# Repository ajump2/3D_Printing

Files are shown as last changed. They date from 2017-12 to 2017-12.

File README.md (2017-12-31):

# Introduction
I'm running a modified Prusa i3 using two e3D v6s on a Bowden setup, originally this printer was built from a reprapguru kit found [here](https://reprapguru.com/). Any and all gcode is made using Slicer or Cura, and modified using a text editor so the fan runs constantly.

# Bowden Dual Extruder Installation
## 3D-Printed Parts
* 2 x [extruder mounts](https://www.thingiverse.com/thing:2078038)
* 2 x [x-carriage mount](https://www.thingiverse.com/thing:1065471)

The x-carriage mount fits the standard Prusa i3 x-carriage, like the one modeled [here](https://www.thingiverse.com/thing:399130) (So no need to install a new x-carriage). I'm also gonna suggest that you print two of the x-carriage mounts, in case one breaks.

## Materials
* Additional Extruder motor (I repurposed the ones from [here](https://www.amazon.com/Geeetech-Dual-Extruder-hotend-nozzle/dp/B075TGY28F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), and you can use the direct drive system if you'd like, although I had a number of issues with it)
* 1 x [RRD fan extender](https://www.amazon.com/AuBreey-Extender-DUAL-EXTRUSION-Printer-Reprap/dp/B07115SX39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)
* 2 x [PTFE fittings](https://www.amazon.com/dp/B01F1XTRGI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)
* 2 x [e3d v6s](https://www.amazon.com/E3D-All-metal-HotEnd-Full-Approximately/dp/B00NAK9JFO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)

Please note that while these parts satisfy the minimum requirement, redundancies are recommended. The e3D thermistors are sensitive, and can crack very easily. Also note that you'll want to heat the hot ends up before removing the heat breaks (which you'll have to do as you're troubleshooting).

## Electronic/Mechanical Configuration
In-Progress

### Wiring
The RRD extender fits on the Aux 1 pins, where you can follow the below diagram for wiring.

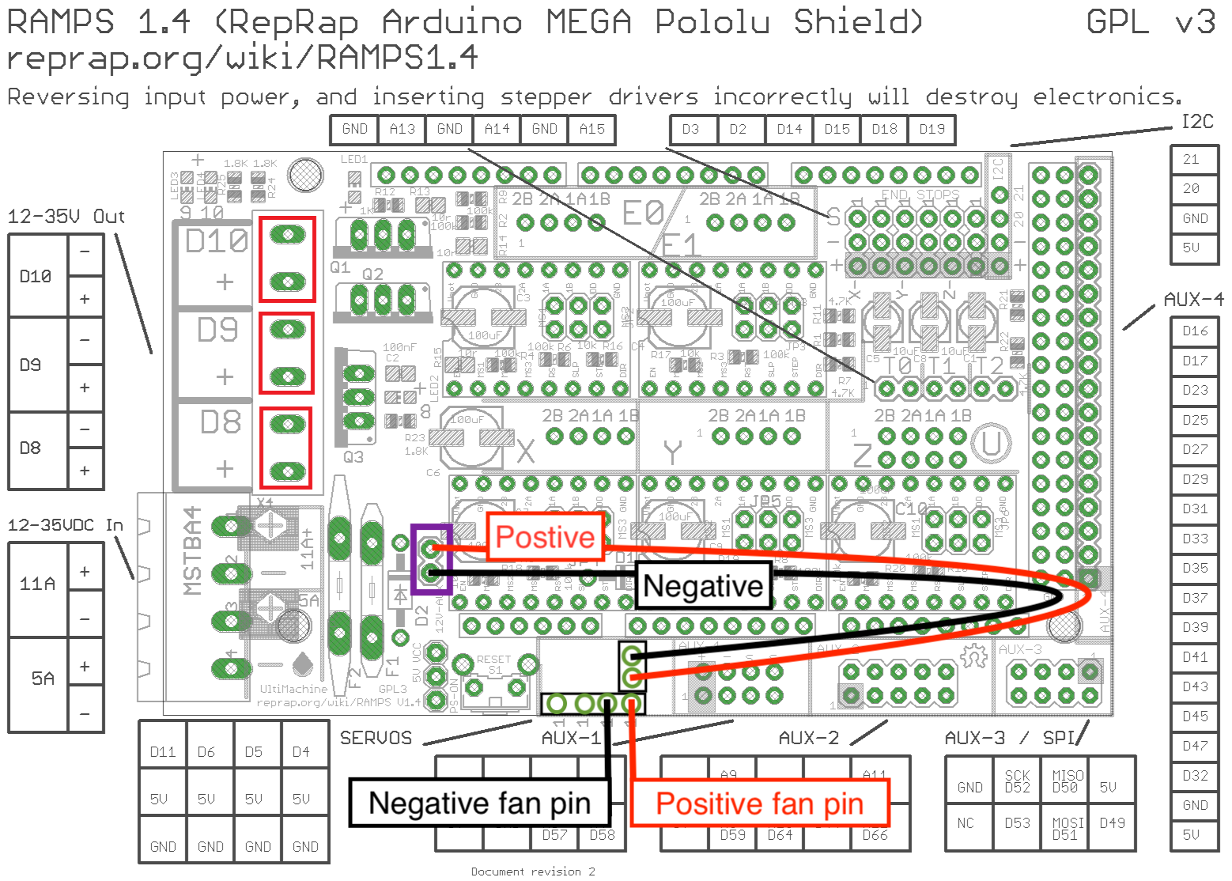
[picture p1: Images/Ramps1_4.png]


This frees the D9 pin (where the fan was connected) for use by the second extruder heater cartridge. As with the first extruder, polarity is not important. The extruder motor connects to the E1 pins (above where the first extruder is connected). Then you'll want to connect the second extruders thermistor to space T2. This can all be seen in the below diagram.

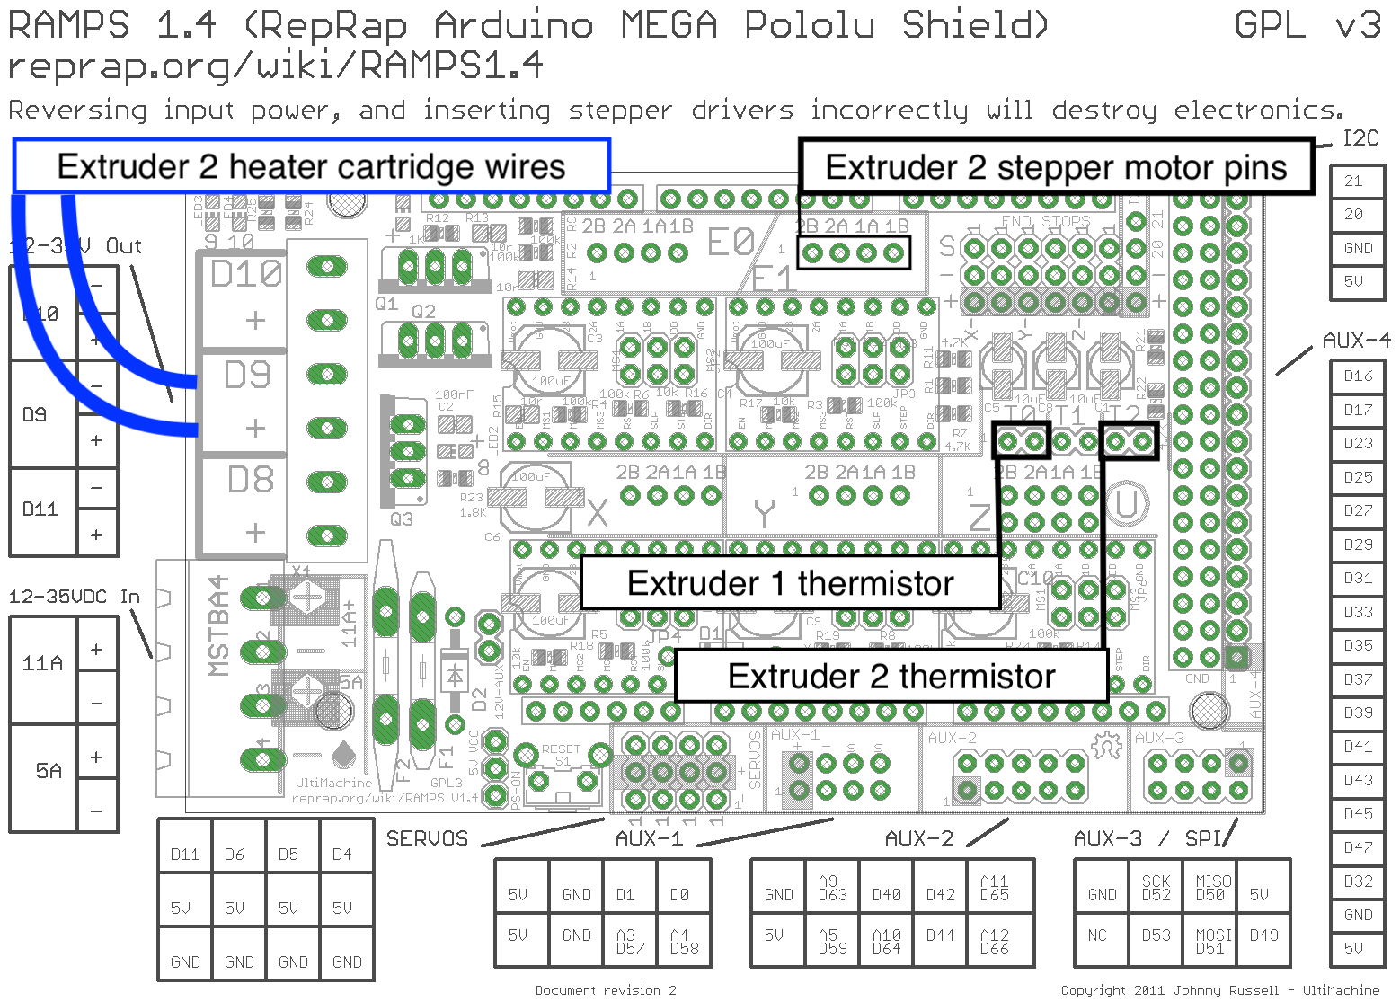
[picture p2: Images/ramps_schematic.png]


Other than the wiring shown here, the ramps board should be wired in the exact same way as for the single extruder setup.

## Firmware/Mechanical Configuration
My marlin files are included in this repository, [here](https://github.com/ajump2/3D_Printing/tree/master/Marlin). Note that the second fan doesn't work (I believe it's a problem with my RRD board), which you can use [this](https://www.geeetech.com/wiki/index.php/Reprap_Ramps1.4_RRD_Fan_Extender) code to test.

``` arduino
void setup() {
 pinMode(11, OUTPUT);
 pinMode(6, OUTPUT);
}

void loop() {
 digitalWrite(11, HIGH);
 digitalWrite(6, LOW);
 delay(5000);
 digitalWrite(11, LOW);
 digitalWrite(6, HIGH);
 delay(5000);
}
```

You'll want to change your motherboard settings found in configuration.h

``` arduino
#ifndef MOTHERBOARD
#define MOTHERBOARD 34
#endif

#define EXTRUDERS 2

#define EXTRUDER_OFFSET_X {0.0, -8.5} // (in mm) for each extruder, offset of the hotend on the X axis
#define EXTRUDER_OFFSET_Y {0.0, 0.0} // (in mm) for each extruder, offset of the hotend on the Y axis
```

Likewise, you'll need to define the number of extruders in Configuration_adv.h

``` arduino
//===========================================================================
//=============================Mechanical Settings===========================
//===========================================================================

// This defines the number of extruders
#define EXTRUDERS 2
```

Since the fan is no longer defined on D9, in pins.h you'll need to change the section,

``` arduino
#if MOTHERBOARD == 33 || MOTHERBOARD == 34
...
#endif// MOTHERBOARD == 33 || MOTHERBOARD == 34
```
to the following,
``` arduino
#define X_STEP_PIN         54
#define X_DIR_PIN          55
#define X_ENABLE_PIN       38
#define X_MIN_PIN           3
#define X_MAX_PIN           2   //2 //Max endstops default to disabled "-1", set to commented value to enable.

#define Y_STEP_PIN         60
#define Y_DIR_PIN          61
#define Y_ENABLE_PIN       56
#define Y_MIN_PIN          14
#define Y_MAX_PIN          15   //15

#define Z_STEP_PIN         46
#define Z_DIR_PIN          48
#define Z_ENABLE_PIN       62
#define Z_MIN_PIN          18
#define Z_MAX_PIN          19

#define Z2_STEP_PIN        36
#define Z2_DIR_PIN         34
#define Z2_ENABLE_PIN      30

#define E0_STEP_PIN        26
#define E0_DIR_PIN         28
#define E0_ENABLE_PIN      24

#define E1_STEP_PIN        36
#define E1_DIR_PIN         34
#define E1_ENABLE_PIN      30

#define SDPOWER            -1
#define SDSS               53
#define LED_PIN            13

#if MOTHERBOARD == 33
#define FAN_PIN            9 // (Sprinter config)
#else
#define FAN_PIN            6 // IO pin. Buffer needed
#endif
#define PS_ON_PIN          12

#ifdef REPRAP_DISCOUNT_SMART_CONTROLLER
#define KILL_PIN           41
#else
#define KILL_PIN           -1
#endif

#define HEATER_0_PIN       10   // EXTRUDER 1
#if MOTHERBOARD == 33
#define HEATER_1_PIN       -1
#else
#define HEATER_1_PIN       9    // EXTRUDER 2 (FAN On Sprinter)
#endif
#define HEATER_2_PIN       -1
#define TEMP_0_PIN         13   // ANALOG NUMBERING
#define TEMP_1_PIN         15   // ANALOG NUMBERING
#define TEMP_2_PIN         -1   // ANALOG NUMBERING
#define HEATER_BED_PIN     8    // BED
#define TEMP_BED_PIN       14   // ANALOG NUMBERING

#ifdef ULTRA_LCD

  #ifdef NEWPANEL
     //encoder rotation values
    #define encrot0 0
    #define encrot1 2
    #define encrot2 3
    #define encrot3 1

    #define BLEN_A 0
    #define BLEN_B 1
    #define BLEN_C 2

    #define LCD_PINS_RS 16
    #define LCD_PINS_ENABLE 17
    #define LCD_PINS_D4 23
    #define LCD_PINS_D5 25
    #define LCD_PINS_D6 27
    #define LCD_PINS_D7 29

    #ifdef REPRAP_DISCOUNT_SMART_CONTROLLER
      #define BEEPER 37
      #define BTN_EN1 31
      #define BTN_EN2 33
      #define BTN_ENC 35
      #define SDCARDDETECT 49
    #else
      //arduino pin which triggers an piezzo beeper
      #define BEEPER 33	 // Beeper on AUX-4

      //buttons are directly attached using AUX-2
      #define BTN_EN1 37
      #define BTN_EN2 35
      #define BTN_ENC 31  //the click

      #define SDCARDDETECT -1  // Ramps does not use this port
    #endif

  #else //old style panel with shift register
    //arduino pin witch triggers an piezzo beeper
    #define BEEPER 33		No Beeper added

    //buttons are attached to a shift register
	// Not wired this yet
    //#define SHIFT_CLK 38
    //#define SHIFT_LD 42
    //#define SHIFT_OUT 40
    //#define SHIFT_EN 17

    #define LCD_PINS_RS 16
    #define LCD_PINS_ENABLE 17
    #define LCD_PINS_D4 23
    #define LCD_PINS_D5 25
    #define LCD_PINS_D6 27
    #define LCD_PINS_D7 29

    //encoder rotation values
    #define encrot0 0
    #define encrot1 2
    #define encrot2 3
    #define encrot3 1

    //bits in the shift register that carry the buttons for:
    // left up center down right red
    #define BL_LE 7
    #define BL_UP 6
    #define BL_MI 5
    #define BL_DW 4
    #define BL_RI 3
    #define BL_ST 2

    #define BLEN_B 1
    #define BLEN_A 0
  #endif
#endif //ULTRA_LCD

#else // RAMPS_V_1_1 or RAMPS_V_1_2 as default (MOTHERBOARD == 3)

#define X_STEP_PIN         26
#define X_DIR_PIN          28
#define X_ENABLE_PIN       24
#define X_MIN_PIN           3
#define X_MAX_PIN          -1    //2

#define Y_STEP_PIN         38
#define Y_DIR_PIN          40
#define Y_ENABLE_PIN       36
#define Y_MIN_PIN          16
#define Y_MAX_PIN          -1    //17

#define Z_STEP_PIN         44
#define Z_DIR_PIN          46
#define Z_ENABLE_PIN       42
#define Z_MIN_PIN          18
#define Z_MAX_PIN          -1    //19

#define E0_STEP_PIN         32
#define E0_DIR_PIN          34
#define E0_ENABLE_PIN       30

#define SDPOWER            48
#define SDSS               53
#define LED_PIN            13
#define PS_ON_PIN          -1
#define KILL_PIN           -1

#ifdef RAMPS_V_1_0 // RAMPS_V_1_0
  #define HEATER_0_PIN     12    // RAMPS 1.0
  #define HEATER_BED_PIN   -1    // RAMPS 1.0
  #define FAN_PIN          11    // RAMPS 1.0
#else // RAMPS_V_1_1 or RAMPS_V_1_2
  #define HEATER_0_PIN     10    // RAMPS 1.1
  #define HEATER_BED_PIN    8    // RAMPS 1.1
  #define FAN_PIN           9    // RAMPS 1.1
#endif
#define HEATER_1_PIN        -1
#define HEATER_2_PIN        -1
#define TEMP_0_PIN          2    // MUST USE ANALOG INPUT NUMBERING NOT DIGITAL OUTPUT NUMBERING!!!!!!!!!
#define TEMP_1_PIN          -1
#define TEMP_2_PIN          -1
#define TEMP_BED_PIN        1    // MUST USE ANALOG INPUT NUMBERING NOT DIGITAL OUTPUT NUMBERING!!!!!!!!!
#endif// MOTHERBOARD == 33 || MOTHERBOARD == 34
```

Using Slicer or Cura, adjust your retraction distance to be as short as possible (1mm or so). Also make sure to run the fan at all times. You can do this by changing any M107 commands in your gcode to M106.

Before changing your unit steps in configuration.h, you should test to see if your extruders are working, and try a test using only one extruder.

If underextruding, or the motor skips, or any problems with feeding; go to your RAMPS Board and adjust the stepper drivers for the extruders. By turning the screws you increase the total current for the extruder motors, this is necessary when upgrading from direct drive as the filament has a longer distance to travel.

If this fails, attempt changing heat settings (I've only tested PLA, and I'm running around 190-195C). If both of these steps fail, move on to the next step.

It's also very likely you'll have to change your extruder steps per unit (no need to define for both extruders, defaults to both).

``` arduino
#define DEFAULT_AXIS_STEPS_PER_UNIT   {80,80,4000,130}  // steps per unit (x,y,z,e)
```

# Headset Designs
As part of a research project, several students and I have been working with the [OpenBCI](http://openbci.com/) Ultracortex Mark IV EEG headset. The headset frame is entirely 3D printed, but can be problematic due to the shape. I've used Blender to cut the medium headset into parts, which should aid printing on smaller machines. The use of supports is necessary with any of these headset files, and the overall headset will need to be glued together. For more information on this project, our project code can be found in this [repository](https://github.com/mahn00b/openbci_testing_e).

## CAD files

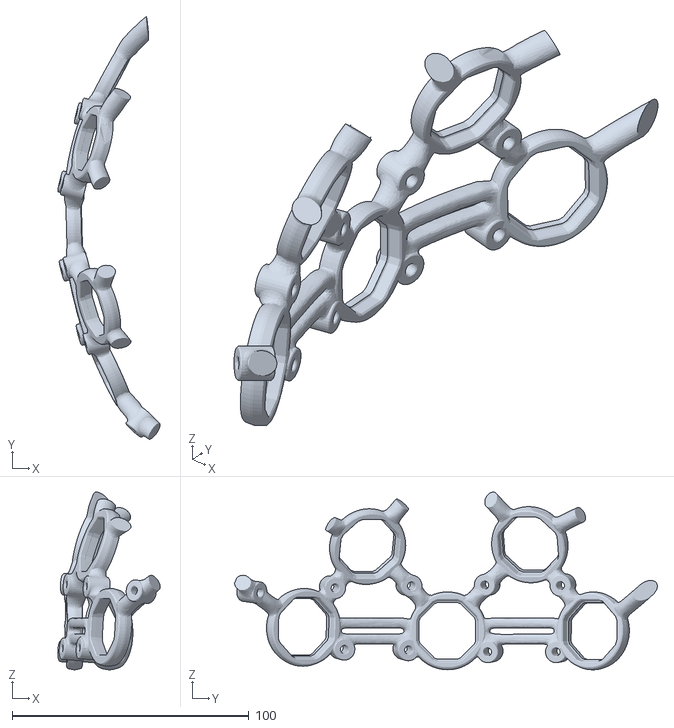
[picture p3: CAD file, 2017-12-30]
Headset_Designs/p1.stl
43.3 x 178.5 x 75.0

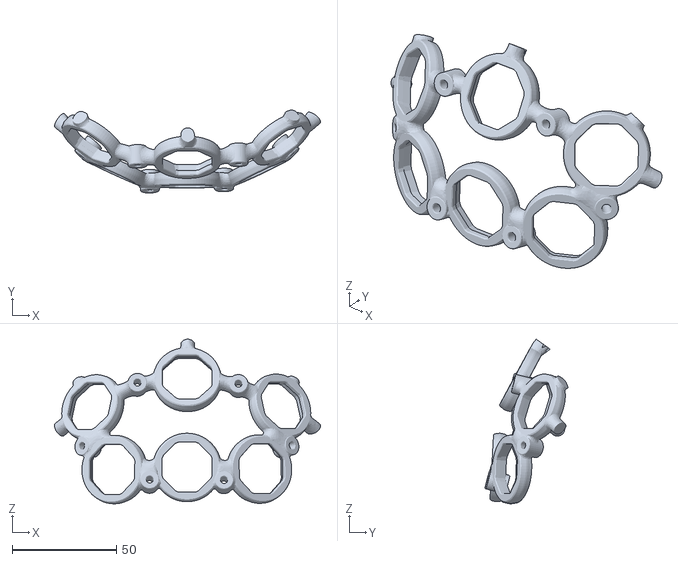
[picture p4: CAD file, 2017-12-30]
Headset_Designs/p3.stl
127.5 x 39.8 x 79.0

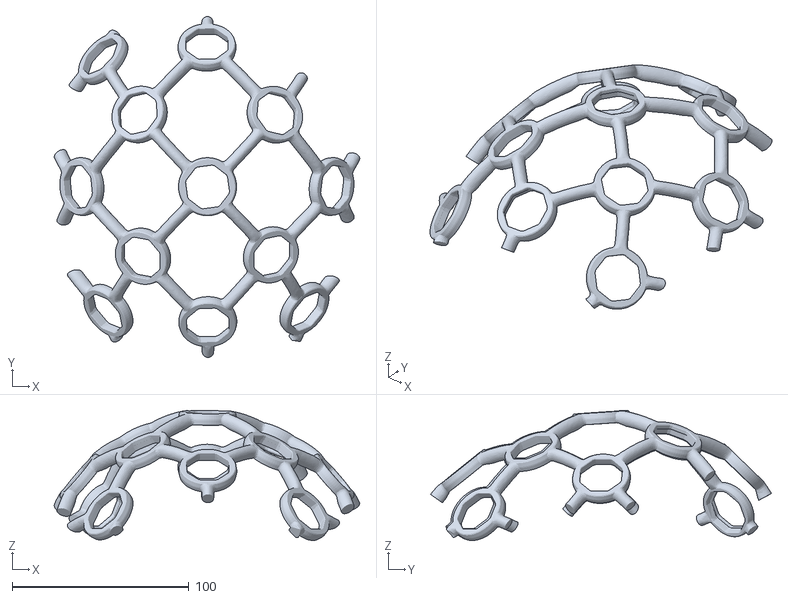
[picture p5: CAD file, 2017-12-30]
Headset_Designs/p5.stl
173.0 x 193.0 x 73.6

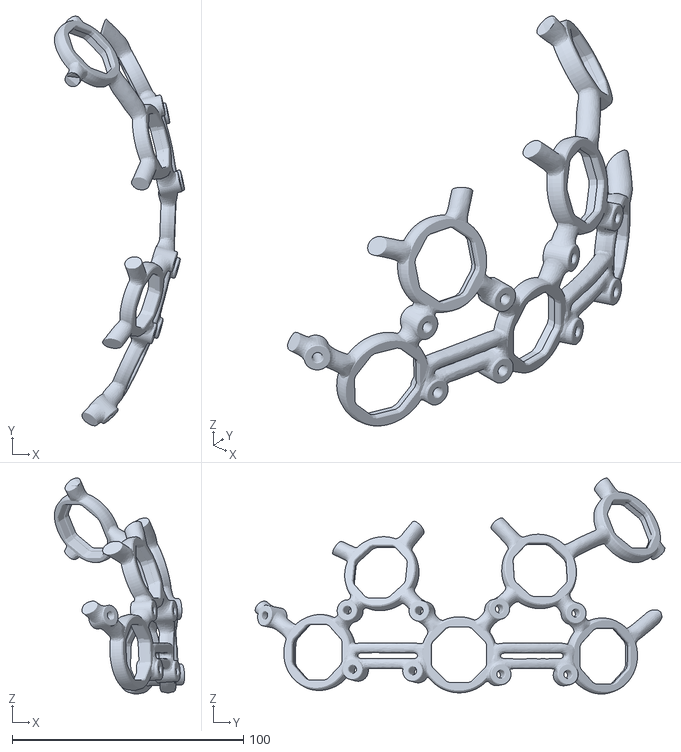
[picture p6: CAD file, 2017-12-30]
Headset_Designs/p4.stl
56.2 x 177.1 x 93.4

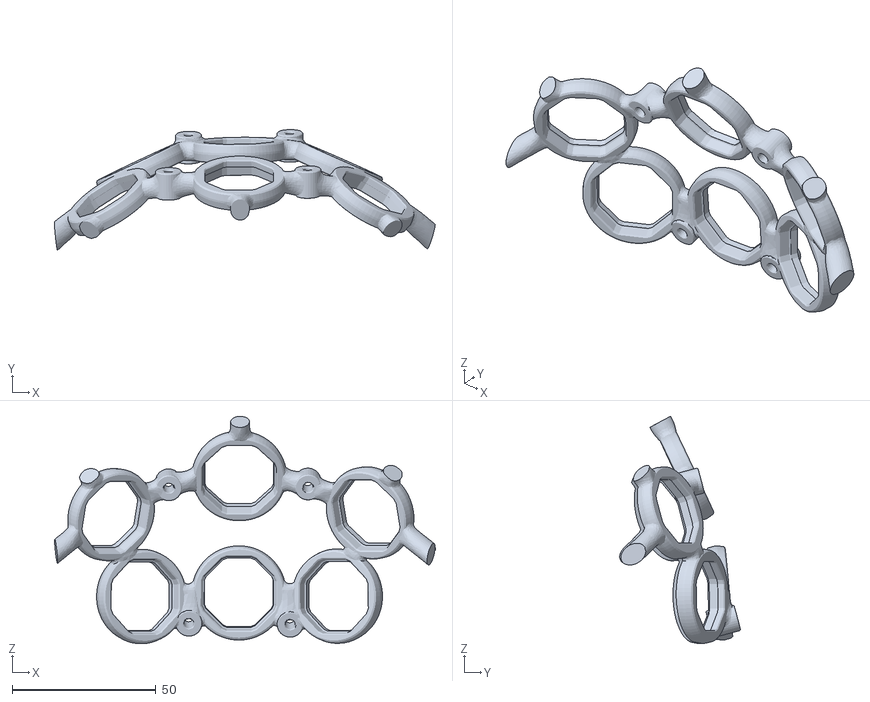
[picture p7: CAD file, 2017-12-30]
Headset_Designs/p2.stl
132.6 x 42.1 x 79.2

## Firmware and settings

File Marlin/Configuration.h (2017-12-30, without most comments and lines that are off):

#include "U8glib.h"
#define CONFIGURATION_H
#define STRING_VERSION_CONFIG_H "2017-12-27" //Personal revision number for changes to THIS file.
#define STRING_CONFIG_H_AUTHOR "Adam Jump" //Who made the changes.
#define SERIAL_PORT 0
#define BAUDRATE 250000
#define MOTHERBOARD 34
#define EXTRUDERS 2
#define EXTRUDER_OFFSET_X {0.0, -8.5} // (in mm) for each extruder, offset of the hotend on the X axis
#define EXTRUDER_OFFSET_Y {0.0, 0.0} // (in mm) for each extruder, offset of the hotend on the Y axis
#define TEMP_SENSOR_0 1
#define TEMP_SENSOR_1 1
#define TEMP_SENSOR_2 1
#define TEMP_SENSOR_BED 1
#define TEMP_RESIDENCY_TIME 10	// (seconds)
#define TEMP_HYSTERESIS 3       // (degC) range of +/- temperatures considered "close" to the target one
#define TEMP_WINDOW     1       // (degC) Window around target to start the recidency timer x degC early.
#define HEATER_0_MINTEMP 5
#define HEATER_1_MINTEMP 5
#define HEATER_2_MINTEMP 5
#define BED_MINTEMP 5
#define HEATER_0_MAXTEMP 275
#define HEATER_1_MAXTEMP 275
#define HEATER_2_MAXTEMP 275
#define BED_MAXTEMP 150
#define PIDTEMP
#define PID_MAX 255 // limits current to nozzle; 255=full current
  #define PID_INTEGRAL_DRIVE_MAX 255  //limit for the integral term
  #define K1 0.95 //smoothing factor withing the PID
  #define PID_dT ((16.0 * 8.0)/(F_CPU / 64.0 / 256.0)) //sampling period of the
    #define  DEFAULT_Kp 63.0
    #define  DEFAULT_Ki 2.25
    #define  DEFAULT_Kd 440
#define MAX_BED_POWER 255 // limits duty cycle to bed; 255=full current
#define PREVENT_DANGEROUS_EXTRUDE
#define PREVENT_LENGTHY_EXTRUDE
#define EXTRUDE_MINTEMP 170
#define EXTRUDE_MAXLENGTH (X_MAX_LENGTH+Y_MAX_LENGTH) //prevent extrusion of very large distances.
#define ENDSTOPPULLUPS // Comment this out (using // at the start of the line) to disable the endstop pullup resistors
  #define ENDSTOPPULLUP_XMIN
  #define ENDSTOPPULLUP_YMIN
  #define ENDSTOPPULLUP_ZMIN
const bool X_ENDSTOPS_INVERTING = true; // set to true to invert the logic of the endstops.
const bool Y_ENDSTOPS_INVERTING = true; // set to true to invert the logic of the endstops.
const bool Z_ENDSTOPS_INVERTING = true; // set to true to invert the logic of the endstops.
#define DISABLE_MAX_ENDSTOPS
#define X_ENABLE_ON 0
#define Y_ENABLE_ON 0
#define Z_ENABLE_ON 0
#define E_ENABLE_ON 0 // For all extruders
#define DISABLE_X false
#define DISABLE_Y false
#define DISABLE_Z false
#define DISABLE_E false // For all extruders
#define INVERT_X_DIR true    // for Mendel set to false, for Orca set to true
#define INVERT_Y_DIR false    // for Mendel set to true, for Orca set to false
#define INVERT_Z_DIR true     // for Mendel set to false, for Orca set to true
#define INVERT_E0_DIR true   // for direct drive extruder v9 set to true, for geared extruder set to false
#define INVERT_E1_DIR false    // for direct drive extruder v9 set to true, for geared extruder set to false
#define INVERT_E2_DIR false   // for direct drive extruder v9 set to true, for geared extruder set to false
#define X_HOME_DIR -1
#define Y_HOME_DIR -1
#define Z_HOME_DIR -1
#define min_software_endstops true //If true, axis won't move to coordinates less than HOME_POS.
#define max_software_endstops true  //If true, axis won't move to coordinates greater than the defined lengths below.
#define X_MAX_POS 200
#define X_MIN_POS 0
#define Y_MAX_POS 200
#define Y_MIN_POS 0
#define Z_MAX_POS 180
#define Z_MIN_POS 0
#define X_MAX_LENGTH (X_MAX_POS - X_MIN_POS)
#define Y_MAX_LENGTH (Y_MAX_POS - Y_MIN_POS)
#define Z_MAX_LENGTH (Z_MAX_POS - Z_MIN_POS)
#define MANUAL_X_HOME_POS 0
#define MANUAL_Y_HOME_POS 0
#define MANUAL_Z_HOME_POS 0
#define NUM_AXIS 4 // The axis order in all axis related arrays is X, Y, Z, E
#define HOMING_FEEDRATE {50*30, 50*30, 4*60, 0}  // set the homing speeds (mm/min)
#define DEFAULT_AXIS_STEPS_PER_UNIT   {80,80,4000,130}  // steps per unit (x,y,z,e)
#define DEFAULT_MAX_FEEDRATE          {250, 250, 2, 22}    // (mm/sec)
#define DEFAULT_MAX_ACCELERATION      {1000,1000,5,1000}    // X, Y, Z, E maximum start speed for accelerated moves. E default values are good for skeinforge 40+, for older versions raise them a lot.
#define DEFAULT_ACCELERATION          500    // X, Y, Z and E max acceleration in mm/s^2 for printing moves
#define DEFAULT_RETRACT_ACCELERATION  500   // X, Y, Z and E max acceleration in mm/s^2 for r retracts
#define DEFAULT_XYJERK                20.0    // (mm/sec)
#define DEFAULT_ZJERK                 0.4     // (mm/sec)
#define DEFAULT_EJERK                 5.0    // (mm/sec)
#define REPRAP_DISCOUNT_SMART_CONTROLLER
 #define ULTIPANEL
 #define NEWPANEL
  #define NEWPANEL  //enable this if you have a click-encoder panel
  #define SDSUPPORT
  #define ULTRA_LCD
  #define LCD_WIDTH 20
  #define LCD_HEIGHT 4
  #define PLA_PREHEAT_HOTEND_TEMP 180
  #define PLA_PREHEAT_HPB_TEMP 70
  #define PLA_PREHEAT_FAN_SPEED 255		// Insert Value between 0 and 255
  #define ABS_PREHEAT_HOTEND_TEMP 240
  #define ABS_PREHEAT_HPB_TEMP 100
  #define ABS_PREHEAT_FAN_SPEED 255		// Insert Value between 0 and 255
#include "Configuration_adv.h"
#include "thermistortables.h"

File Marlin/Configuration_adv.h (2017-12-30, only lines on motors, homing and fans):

#define ENDSTOPS_ONLY_FOR_HOMING // If defined the endstops will only be used for homing
#define X_HOME_RETRACT_MM 5
#define Y_HOME_RETRACT_MM 5
#define Z_HOME_RETRACT_MM 1

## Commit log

2017-12-30 added headset files
    [p1.stl, p2.stl, p3.stl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]
2017-12-30 Added Marlin Files
    [Configuration.h, Configuration_adv.h, Menu Plans.xlsx]
2017-12-30 edited Marlin
2017-12-30 Edit for build instructions
    [Configuration.h]
2017-12-30 Added Wiring Diagram
2017-12-30 added wiring instructions
2017-12-30 added second wiring diagram
2017-12-30 editted for content and second wiring diagram
2018-01-01 Generated using cura, modified to run fan at all times and run fan at 60% speed for the first layer
